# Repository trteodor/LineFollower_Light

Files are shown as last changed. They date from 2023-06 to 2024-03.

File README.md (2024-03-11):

# Light Follower Light

**_ "Robot" which follow for a black line on a white theme _**

⭐ Collecting stars ⭐ - If you liked this project, please leave a star here

Demonstration videos:

Jsumo wheels vs solarbotics:
https://www.youtube.com/watch?v=5hosZAXFKjE

X_Challange 2023, Rzeszow:
https://www.youtube.com/watch?v=OcwFzTCTTZQ

New JSumo Tires test:
https://youtu.be/Sj1vxMwn7Ys (achived average speed 1.8m/s!)

Real world prototypes:    ( Jsumo and Solarbotics wheels )

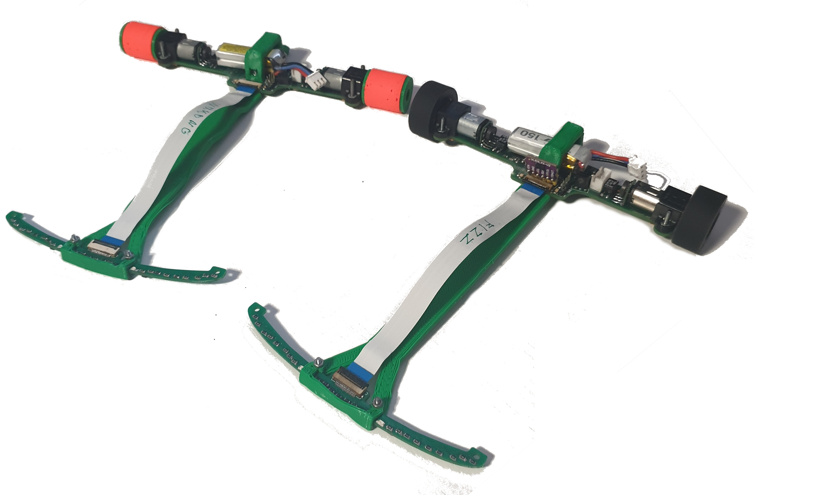
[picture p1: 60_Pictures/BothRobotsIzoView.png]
FristPrototypePhoto


Simulated assembly izometric view:

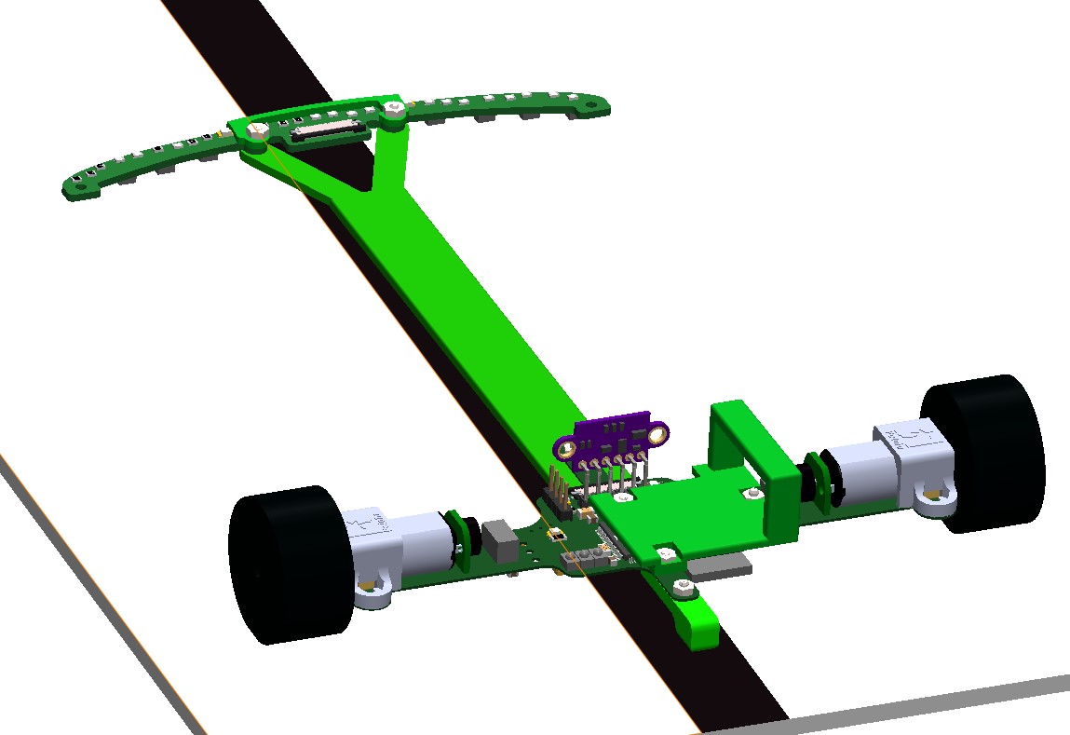
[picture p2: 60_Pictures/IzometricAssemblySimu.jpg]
Izometric3D_View


  * You will need to spend around 200$ if you want recreate this design (PCB order included)
  * most important parts list: 10_PCB_Hardware_Altium\Readme.md

In Embedded source code is implemented many algorithms, PID Controller is used to follow for the black line on white theme.

Nevertheless many things still can be done better. Let's be honest - the prepared Control Code in my opinion is somewhere between a draft and a prototype

# In this project:

PCB and 3D Assemblyis prepared, real world prototype prepared

TODO:
* Add support for MPU-6050
* Add support for VL53l0
* Development of QT service application..
* Generally much things..

# -------------------------------------------------------
The repository contains all the files used to create this project (PCB, Mechanic models, Embedded source Code, QT serv. App code)

QT service app overview screen shot:

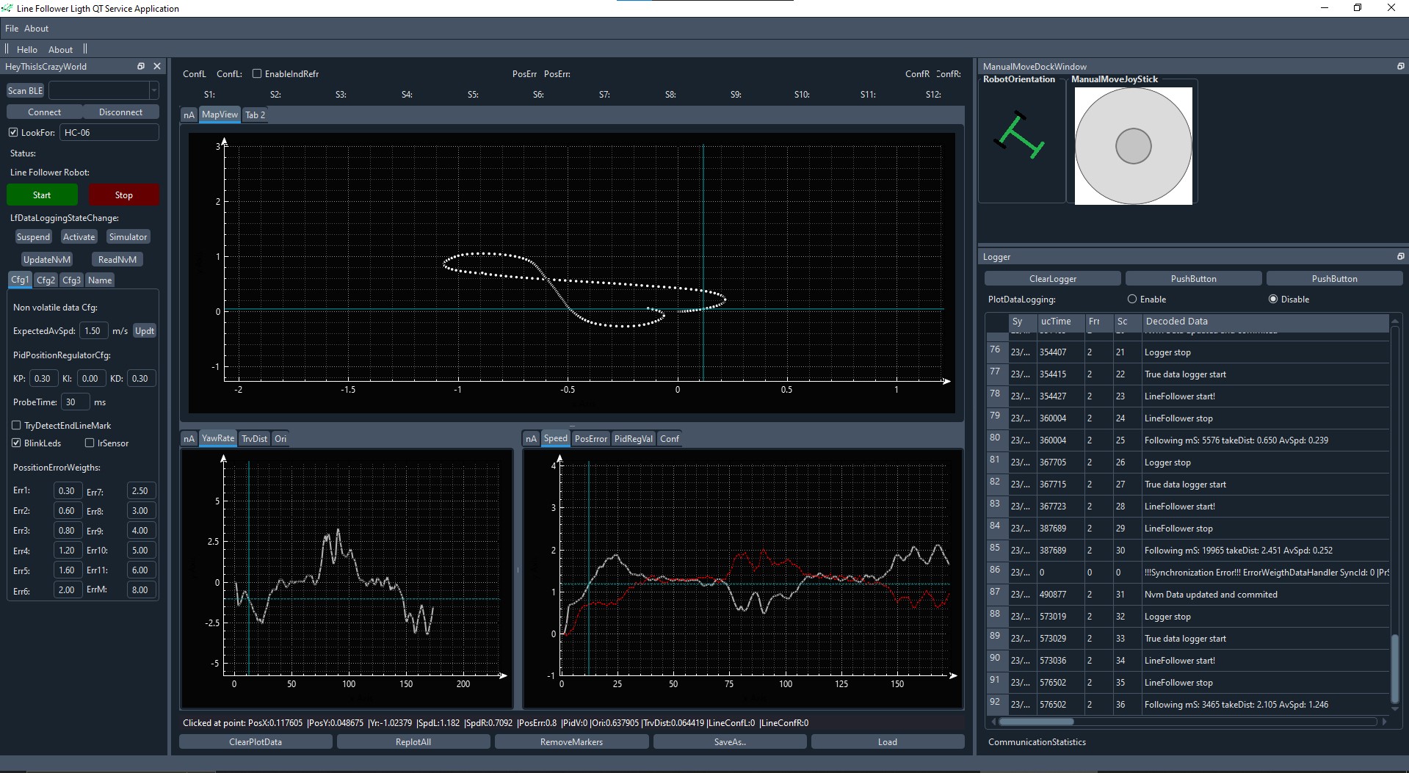
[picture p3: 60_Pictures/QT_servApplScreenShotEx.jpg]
QtApp


Installer wizard:  (created using Inno Compiler)
https://github.com/trteodor/LineFollower_Light/blob/master/40_ServiceApplication_QT/LF_ServiceApp_1.35_Installer.exe

After installation associated "*.lfp" extension should be opened by default by LF_ServiceApp"

Highlevel Overview:

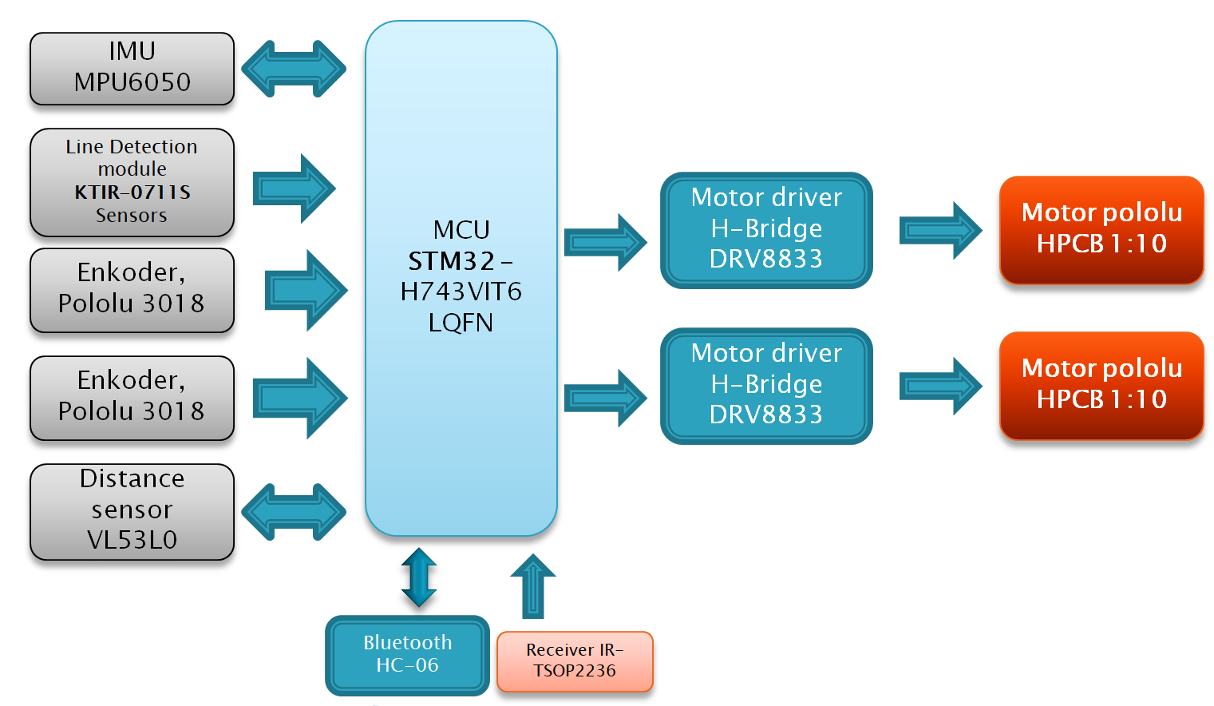
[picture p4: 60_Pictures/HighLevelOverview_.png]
HighLevelOverview


Repository size:

 ~500MB

# References
* https://github.com/trteodor/Line_Follower_STM32H7
* https://forbot.pl/blog/algorytm-linefollowera-c-poczatkujacych-id2722
* https://kcir.pwr.edu.pl/~mucha/Pracki/Jedrzej_Stolarz_praca_inzynierska.pdf
* https://kcir.pwr.edu.pl/~mucha/Pracki/Witek_Lipieta_praca_magisterska.pdf
* https://kcir.pwr.edu.pl/~mucha/Pracki/Rafal_Cyminski_praca_magisterska.pdf
* https://forbot.pl/forum/topic/13552-cukiereczek/

**_If you have questions, please open an issue in this repository or comment below the YouTube video._**

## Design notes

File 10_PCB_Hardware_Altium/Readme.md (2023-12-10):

Altium Designer viewer - is free, use it to view schematics and PCB.

Production files are attached in appropriate folders.

Attached data is sufficient to create production files for PCB (Gerber Files) or for reverse engineering. Modifications to schematics and PCBs are also possible.

Some of the most important items or items not shown in the altium schematics:
* https://botland.com.pl/enkodery/4884-zestaw-enkoderow-magnetycznych-do-micro-silnikow-pololu-kompatybilne-z-hpcb-27-18v-2-szt-pololu-3081.html
* https://botland.com.pl/silniki-dc-micro-z-przekladnia/4974-silnik-hpcb-101-obustronny-wal-pololu-3071.html
* https://www.tme.eu/pl/details/ffc0520150/tasmy-ffc-fpc/riverdi/
* https://www.tme.eu/pl/details/mx-15266-0209/tasmy-ffc-fpc/molex/15266-0209/
* https://botland.com.pl/kola-z-oponami/24-kolo-solarbotics-rw2i-mocowane-wewnetrznie-pololu-1127.html
* https://abc-rc.pl/product-pol-7891-Modul-BMS-PCM-PCB-ladowania-i-ochrony-ogniw-Li-ion-2S-8-4V-5A-18650.html (to get lion protection circuit elements)
* https://botland.com.pl/akumulatory-li-pol-2s-74v-/8973-pakiet-li-pol-dualsky-250mah-30c-2s-74v-eco-s-6941047104631.html or
* https://botland.com.pl/akumulatory-li-pol-2s-74v-/8248-pakiet-li-pol-dualsky-150mah-30c-2s-74v-eco-s-6941047106321.html 
* https://www.tme.eu/pl/details/cmj2101/dlawiki-smd-pozostale/talema/cmj-2-101/
* Distance sensor VL53
* https://kamami.pl/moduly-bluetooth/211365-modul-bluetooth-hc-06-20edr.html

Currently wheels are created using tires ordered here:
* https://www.jsumo.com/js2042-silicone-wheel-without-rim-1-pair
Although, I would recommend you to start with solarbotics wheels

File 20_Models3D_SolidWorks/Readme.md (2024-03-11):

In directory 23_STL are located OutPout files(to print on 3d printer). You can find there relased mechanical 3D STL - files which can be printed using 3D Printer...

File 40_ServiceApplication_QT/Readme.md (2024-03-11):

I'm not familiar with the QT framework, the application is my frist GUI app. Sorry for the style, magic numbers, etc.. 

Despite that, hopefully the source code is readable.

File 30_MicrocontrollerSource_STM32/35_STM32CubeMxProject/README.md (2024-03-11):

To compile MCU Source code you can use STM32CubeIDE or makefiles(GNUmake + arm-none-eabi-gcc)

Used MCU: STM32H743VITx
LQFP100

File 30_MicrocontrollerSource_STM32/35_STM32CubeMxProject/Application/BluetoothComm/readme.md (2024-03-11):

This is Bluetooth low energy module to communicate wirelessly between PC and LineFollower robot

Bluetooth Module: HC-06

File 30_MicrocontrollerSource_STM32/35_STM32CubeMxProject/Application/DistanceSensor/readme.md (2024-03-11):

Not supported(todo)

It's possible to mount a VL53 sensor to detected and omit obstacles.

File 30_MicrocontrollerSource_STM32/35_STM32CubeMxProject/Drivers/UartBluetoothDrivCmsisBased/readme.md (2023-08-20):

Due to some confusion while using HAL libary, it has been decided to implement own simple uart driver to communicate with Bluetooth module.

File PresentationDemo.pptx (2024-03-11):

## My Construction of Line Follower robot

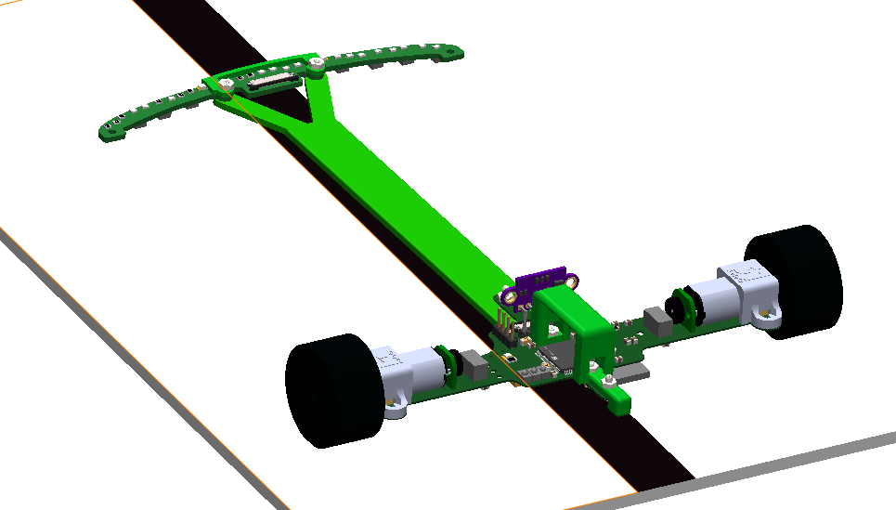
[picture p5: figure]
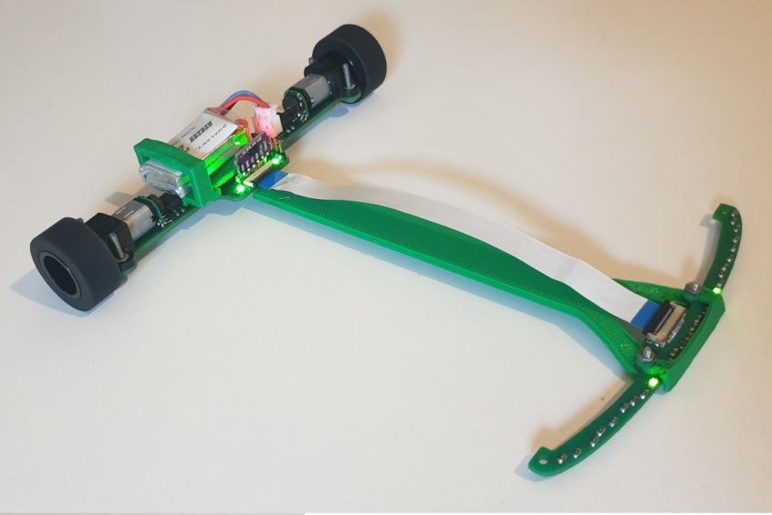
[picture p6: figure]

## Demo video:

Experiments in house environment
- https://www.youtube.com/watch?v=5hosZAXFKjE
Robot competition „X_Challange 2023, Rzeszow”:
- https://www.youtube.com/watch?v=OcwFzTCTTZQ

## Electrical structure:

- The electrical structure of the vehicle model is made from designed printed circuits in Altium Designer:

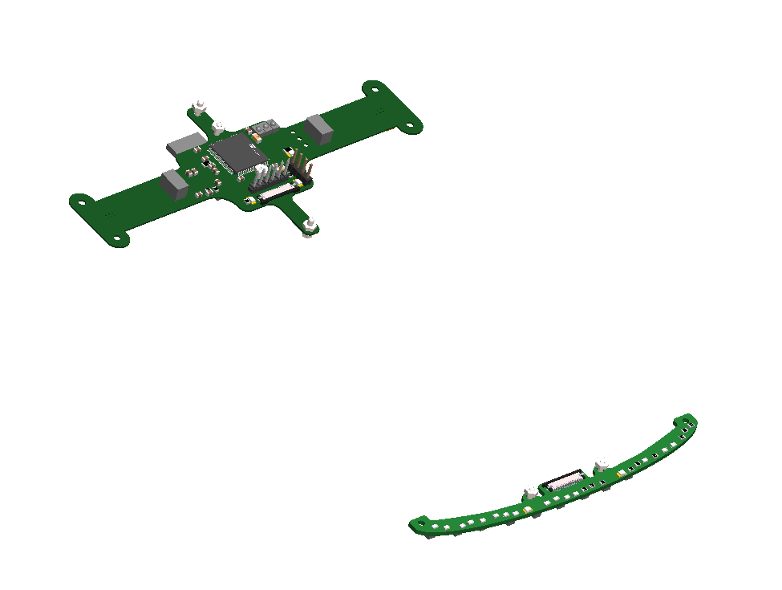
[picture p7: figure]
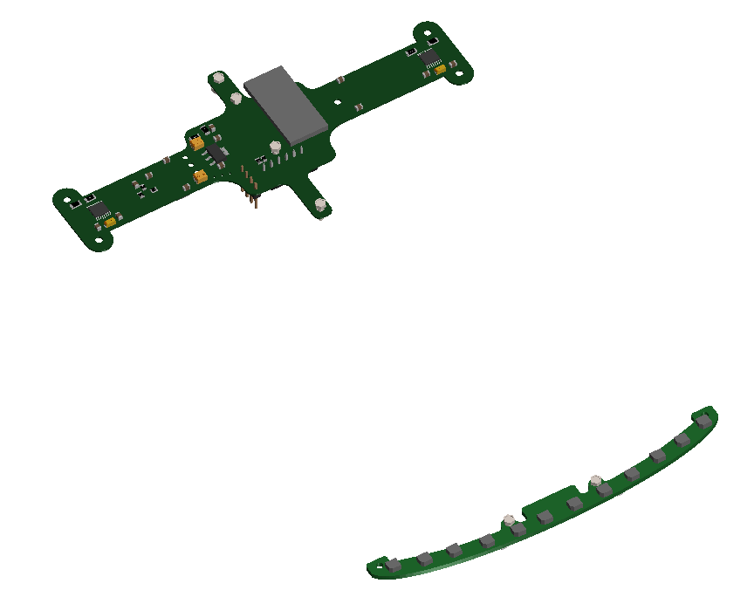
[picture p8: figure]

## Skeleton and connection

- The 3D model of robot has been designed using Solidworks
- In the next step – designed parts were printed on 3D Printer.

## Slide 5

High level overview, hardware blocks

IMU
MPU6050

Line Detection module
KTIR-0711S Sensors

Enkoder,
Pololu 3018

MCU STM32 -H743VIT6
LQFN

Motor driver
H-Bridge
DRV8833

Motor pololu
HPCB 1:10

Enkoder,
Pololu 3018

Motor driver
H-Bridge
DRV8833

Motor pololu
HPCB 1:10

Distance sensor
VL53L0

Bluetooth
HC-06

Receiver IR-
TSOP2236

## Practical realization:

Solarbotics wheels:

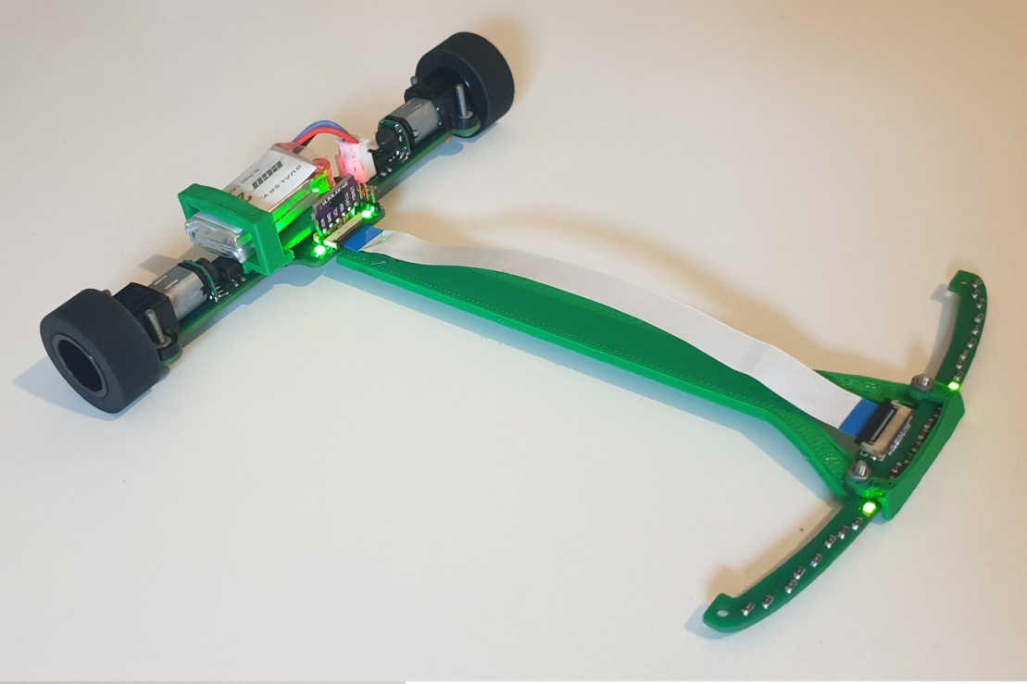
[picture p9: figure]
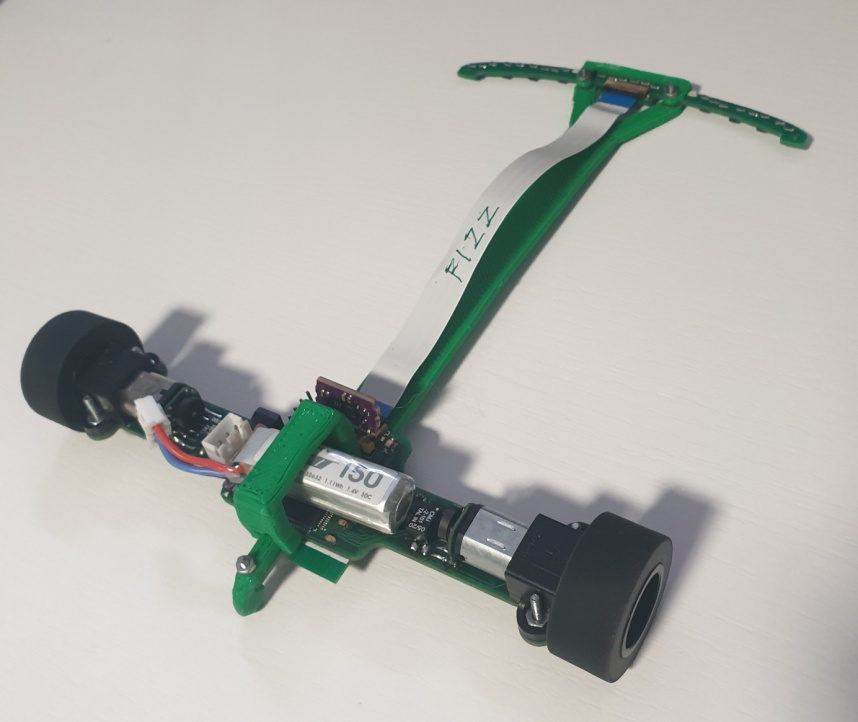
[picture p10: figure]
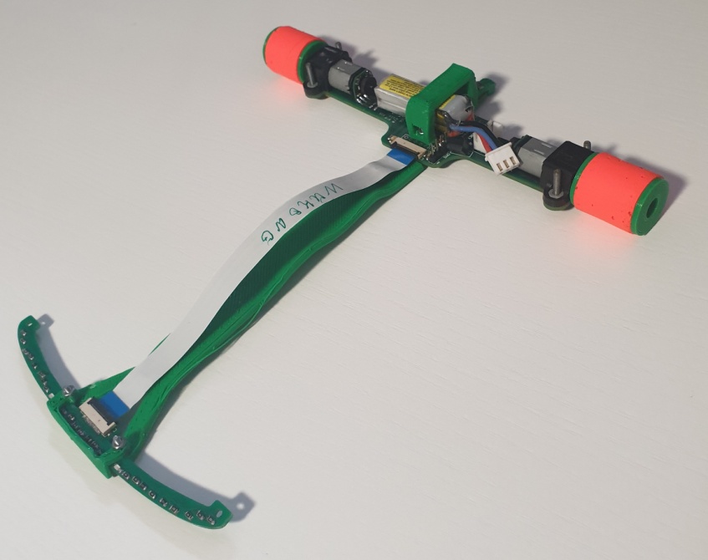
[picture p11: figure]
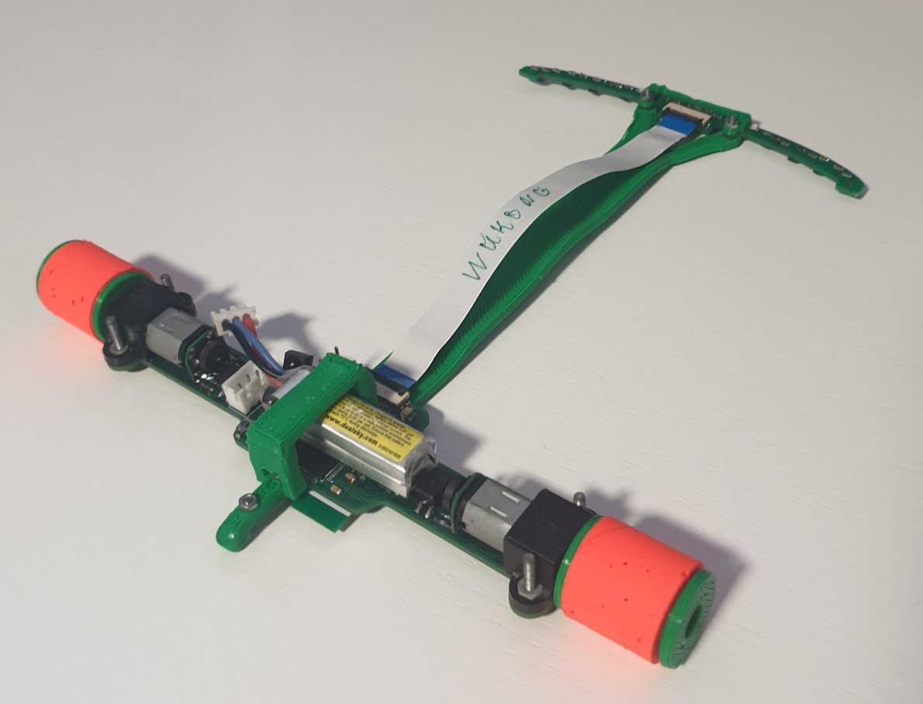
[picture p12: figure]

## Practical realization:

Jsumo wheels:

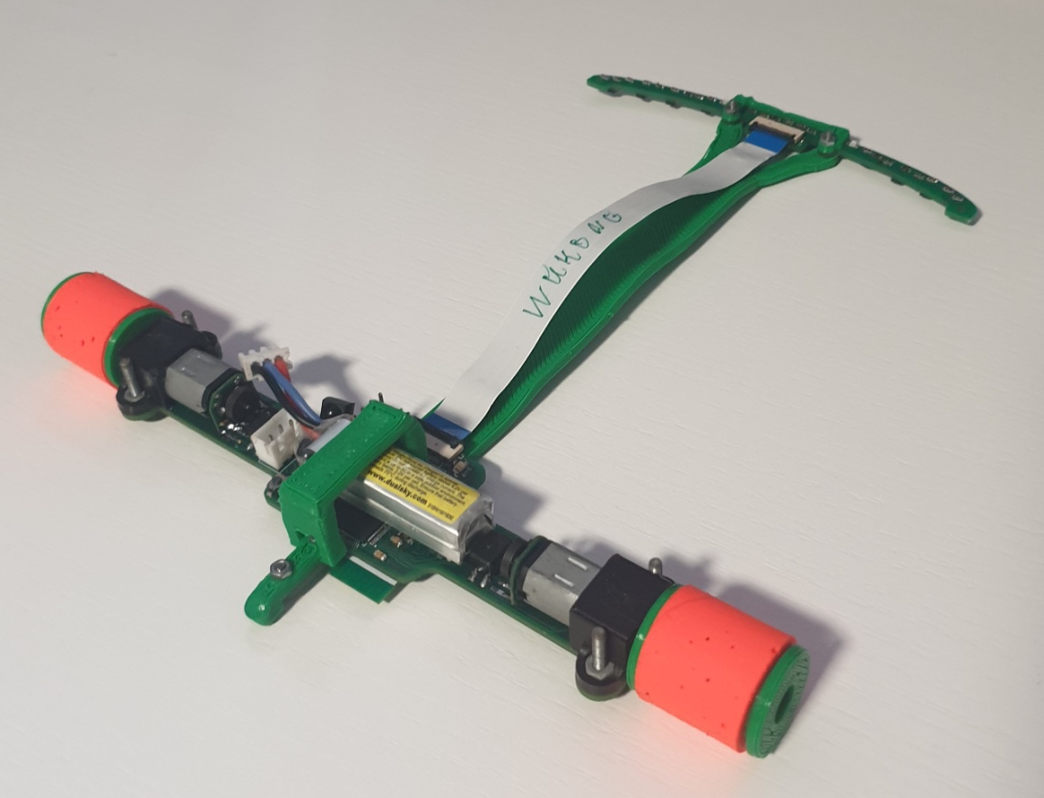
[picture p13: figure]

## Digital representation of the route

- Using the equation below, it is possible to create digital representation of the route.

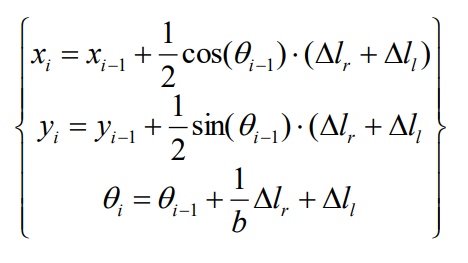
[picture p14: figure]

## Data visualisation, wireless calibration – Windows Desktop App:

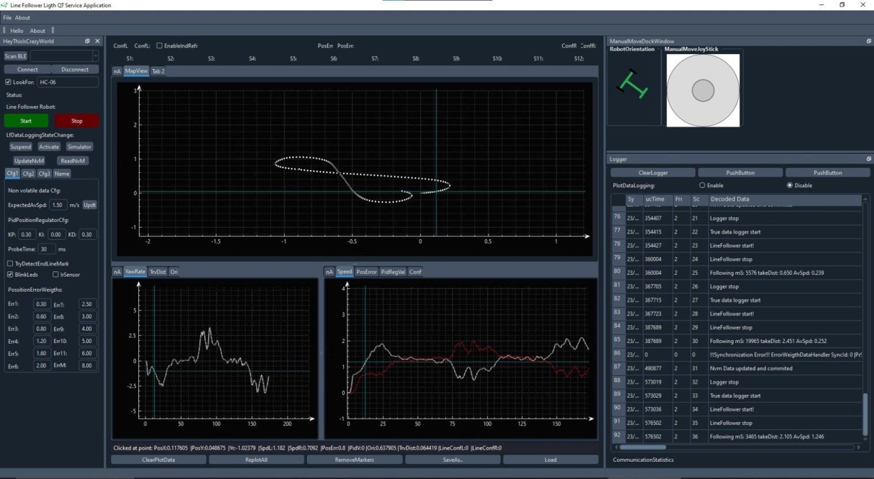
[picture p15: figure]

Designed in QT

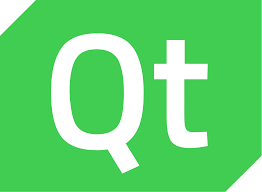
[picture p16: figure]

The app, maybe simply installed:

## It is open source project!

- https://github.com/trteodor/LineFollower_Light
The repository consist:
- MCU Source,
- Schematics, PCB,
- Skeleton(3D elements),
- Documentation,
- everything what is needed to re-create the design/robot.
If you liked the project, please leave a "star" in the repository

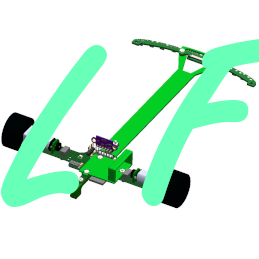
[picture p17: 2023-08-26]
60_Pictures/LF_SimuAsseblyBackSideRightIco.png

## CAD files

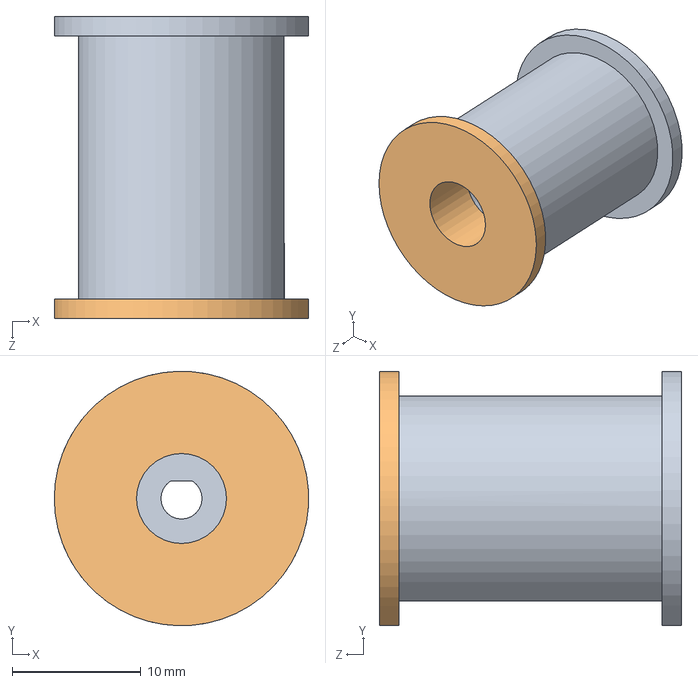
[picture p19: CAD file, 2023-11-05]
20_Models3D_SolidWorks/21_SolidWorksProject/JSummoWheelAsm.SLDASM
19.8 x 19.8 x 23.5 mm
JSumoTireWheel
OutSideCollar

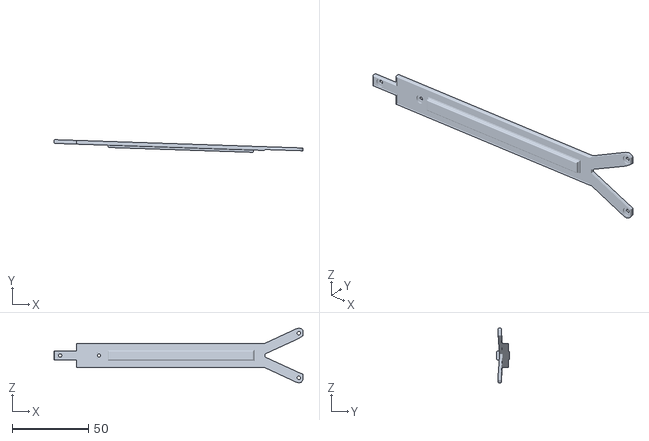
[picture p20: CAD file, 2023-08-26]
20_Models3D_SolidWorks/23_STL - OutPout files( to print on 3d printer)/LF_MB_SB_ConnectorAsm.STL
163.7 x 8.35 x 36.0

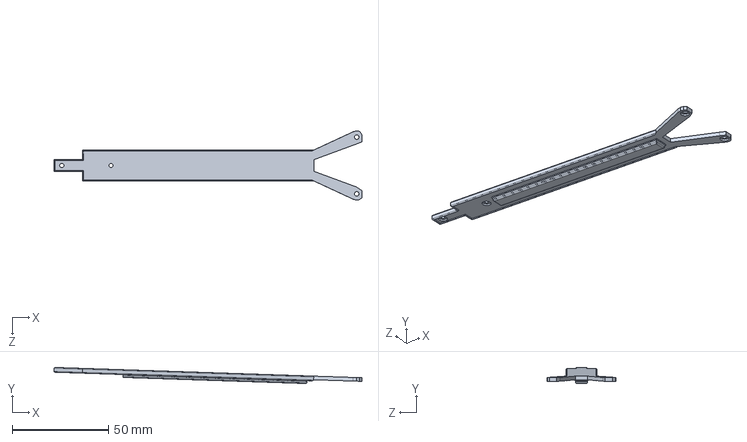
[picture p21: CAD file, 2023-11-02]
20_Models3D_SolidWorks/21_SolidWorksProject/LF_MB_SB_ConnectorAsm.SLDPRT
159.7 x 8.35 x 36.0 mm

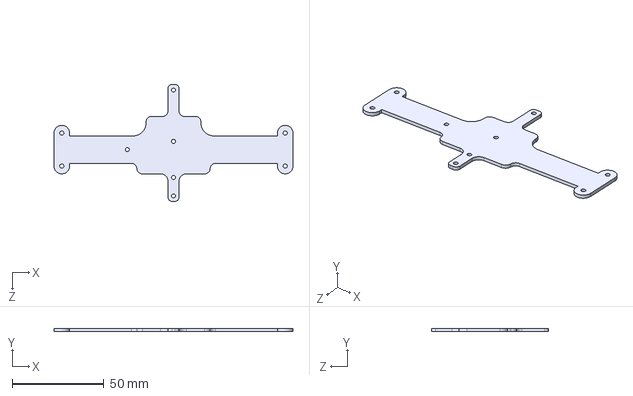
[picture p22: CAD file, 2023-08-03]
20_Models3D_SolidWorks/21_SolidWorksProject/ShapeMainBoardDraft.STEP
130.4 x 1.70 x 63.7 mm

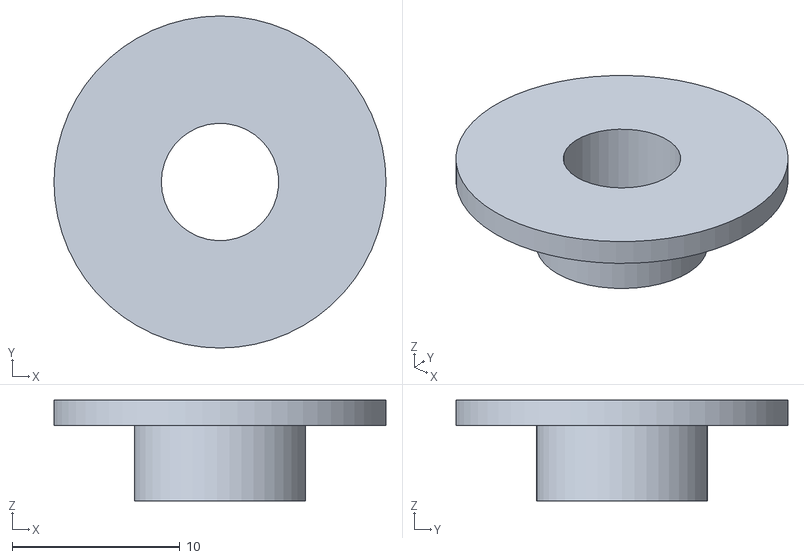
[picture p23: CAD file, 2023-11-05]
20_Models3D_SolidWorks/23_STL - OutPout files( to print on 3d printer)/OutSideCollarJSumoWheel.STL
19.8 x 19.8 x 6.00

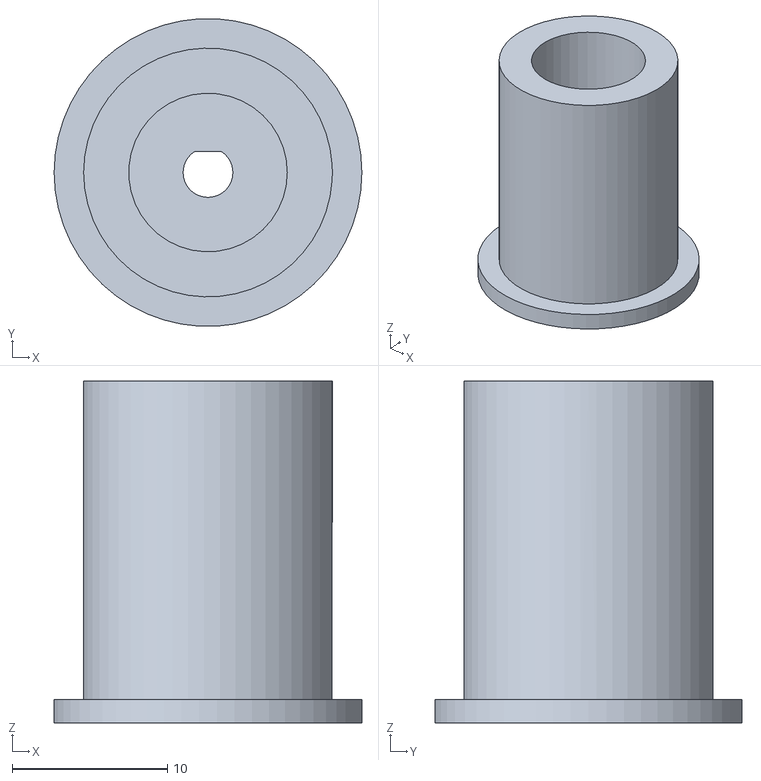
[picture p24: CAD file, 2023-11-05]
20_Models3D_SolidWorks/23_STL - OutPout files( to print on 3d printer)/JSumoTireWheel.STL
19.8 x 19.8 x 22.0

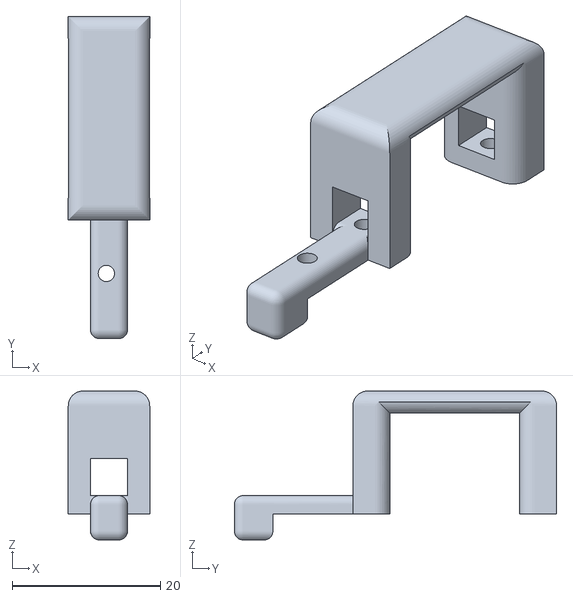
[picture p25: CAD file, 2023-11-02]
20_Models3D_SolidWorks/23_STL - OutPout files( to print on 3d printer)/BatteryHolderJsumo.STL
11.0 x 43.5 x 20.1

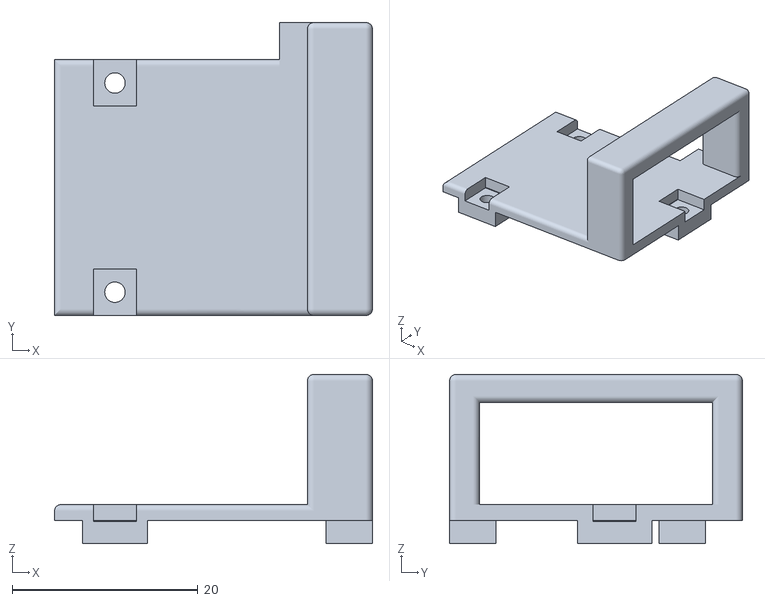
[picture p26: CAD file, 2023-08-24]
20_Models3D_SolidWorks/23_STL - OutPout files( to print on 3d printer)/BatteryHolder.STL
34.2 x 31.5 x 18.2

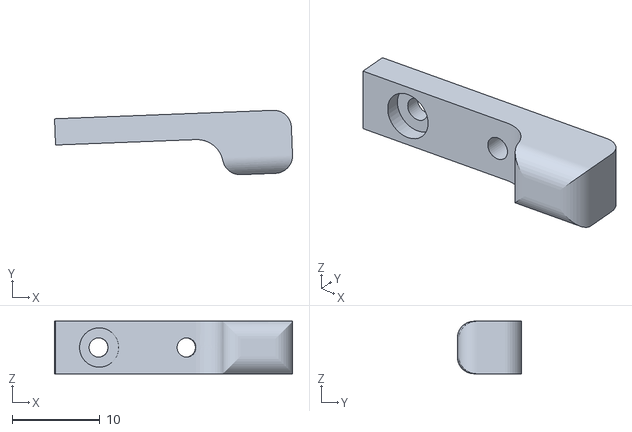
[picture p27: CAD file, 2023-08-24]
20_Models3D_SolidWorks/23_STL - OutPout files( to print on 3d printer)/JumpLiftProtector.STL
27.2 x 7.35 x 6.00

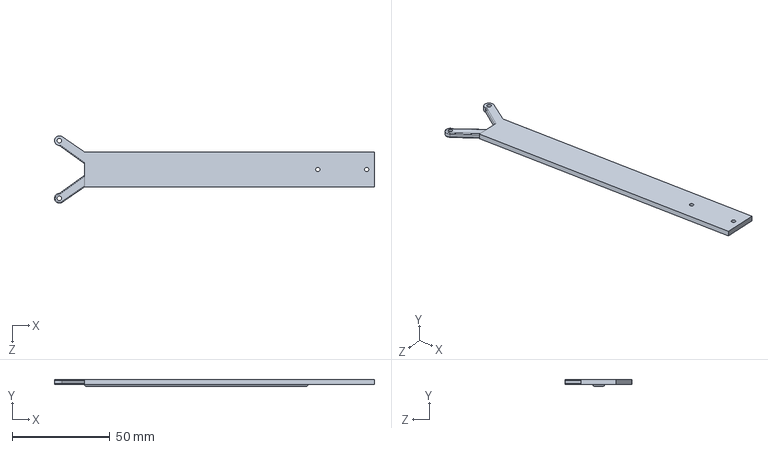
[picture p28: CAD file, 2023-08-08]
20_Models3D_SolidWorks/21_SolidWorksProject/LF_MB_SB_Connector.SLDPRT
163.8 x 3.50 x 34.5 mm

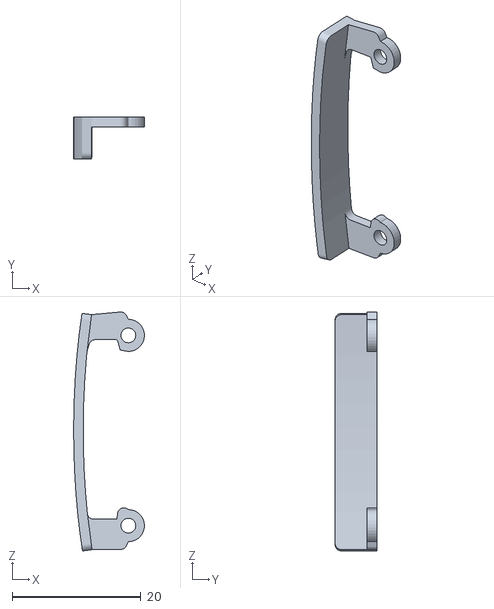
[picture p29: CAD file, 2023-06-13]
20_Models3D_SolidWorks/23_STL - OutPout files( to print on 3d printer)/GroundSlider.STL
11.0 x 6.50 x 37.2

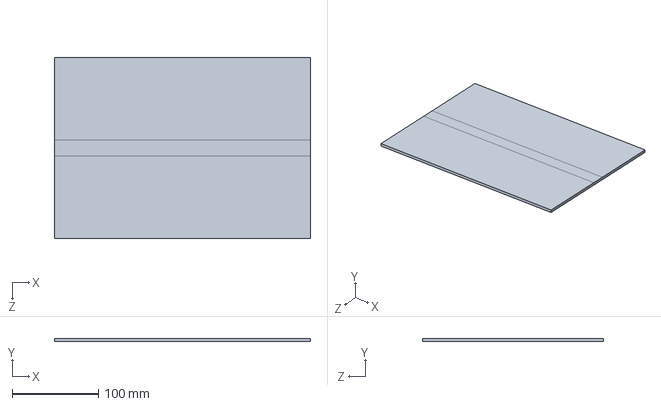
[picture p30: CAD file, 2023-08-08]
20_Models3D_SolidWorks/21_SolidWorksProject/PartOfTruckSimulation.SLDPRT
297.0 x 4.01 x 210.0 mm

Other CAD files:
20_Models3D_SolidWorks/21_SolidWorksProject/OutSideCollar.SLDPRT
20_Models3D_SolidWorks/21_SolidWorksProject/JSumoTireWheel.SLDPRT
20_Models3D_SolidWorks/21_SolidWorksProject/BatteryHolder.SLDPRT
20_Models3D_SolidWorks/21_SolidWorksProject/JumpLiftProtector.SLDPRT
20_Models3D_SolidWorks/21_SolidWorksProject/BatterHolderCl.SLDPRT
20_Models3D_SolidWorks/21_SolidWorksProject/GroundSlider.SLDPRT
20_Models3D_SolidWorks/21_SolidWorksProject/PololuMotorWithEnckodersAndBrackesPlusWheel.STEP
20_Models3D_SolidWorks/21_SolidWorksProject/ShapeMainBoardDraft.SLDPRT
20_Models3D_SolidWorks/21_SolidWorksProject/ShapeSensorBoard.SLDPRT
20_Models3D_SolidWorks/21_SolidWorksProject/ShapeSensorBoard.STEP
20_Models3D_SolidWorks/21_SolidWorksProject/hex head tapping screw_am.SLDPRT
20_Models3D_SolidWorks/21_SolidWorksProject/vl53l0x.STEP

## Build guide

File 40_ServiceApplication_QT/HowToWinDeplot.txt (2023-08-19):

windeployqt.exe --qmldir "...\VirtualJoystickQML" "...\Release_1.1"

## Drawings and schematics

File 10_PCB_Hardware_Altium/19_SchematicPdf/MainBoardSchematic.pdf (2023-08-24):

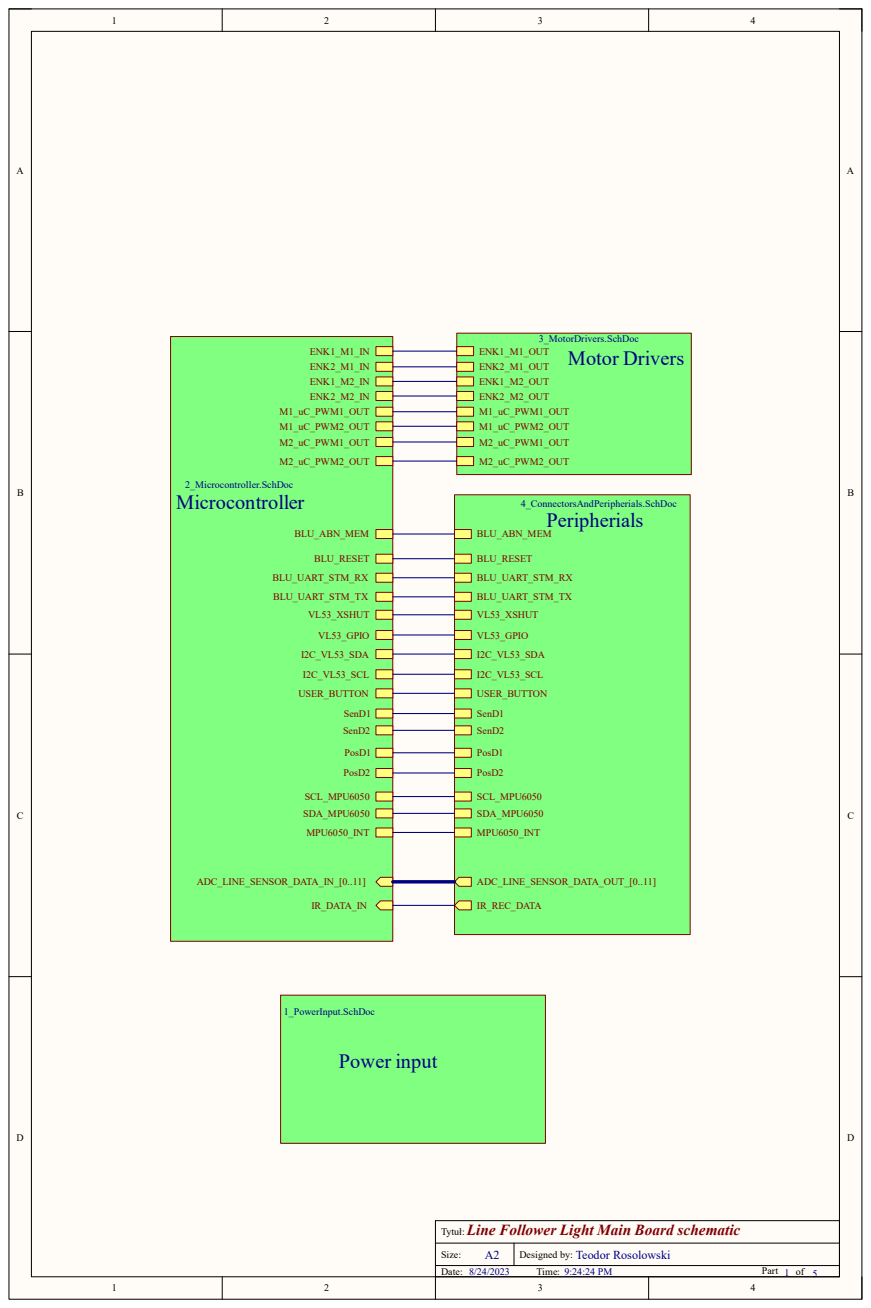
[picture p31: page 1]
Teodor Rosolowski; Size:; Designed by:; Date:; Time:; Part; ENK1_M1_OUT ENK2_M1_OUT ENK1_M2_OUT; M2_uC_PWM1_OUT; ENK2_M2_OUT M1_uC_PWM1_OUT M1_uC_PWM2_OUT; M2_uC_PWM2_OUT; Motor Drivers; 3_MotorDrivers.SchDoc; ADC_LINE_SENSOR_DATA_IN_[0..11]; IR_DATA_IN; MPU6050_INT; SDA_MPU6050; ENK2_M2_IN; ENK1_M2_IN; M1_uC_PWM1_OUT M1_uC_PWM2_OUT; BLU_RESET; BLU_ABN_MEM; ENK1_M1_IN; BLU_UART_STM_TX; ENK2_M1_IN; I2C_VL53_SCL; SenD1; PosD2; SCL_MPU6050; BLU_UART_STM_RX; SenD2; PosD1; VL53_GPIO; VL53_XSHUT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

Line Follower Light Main Board schematic
Tytuł:

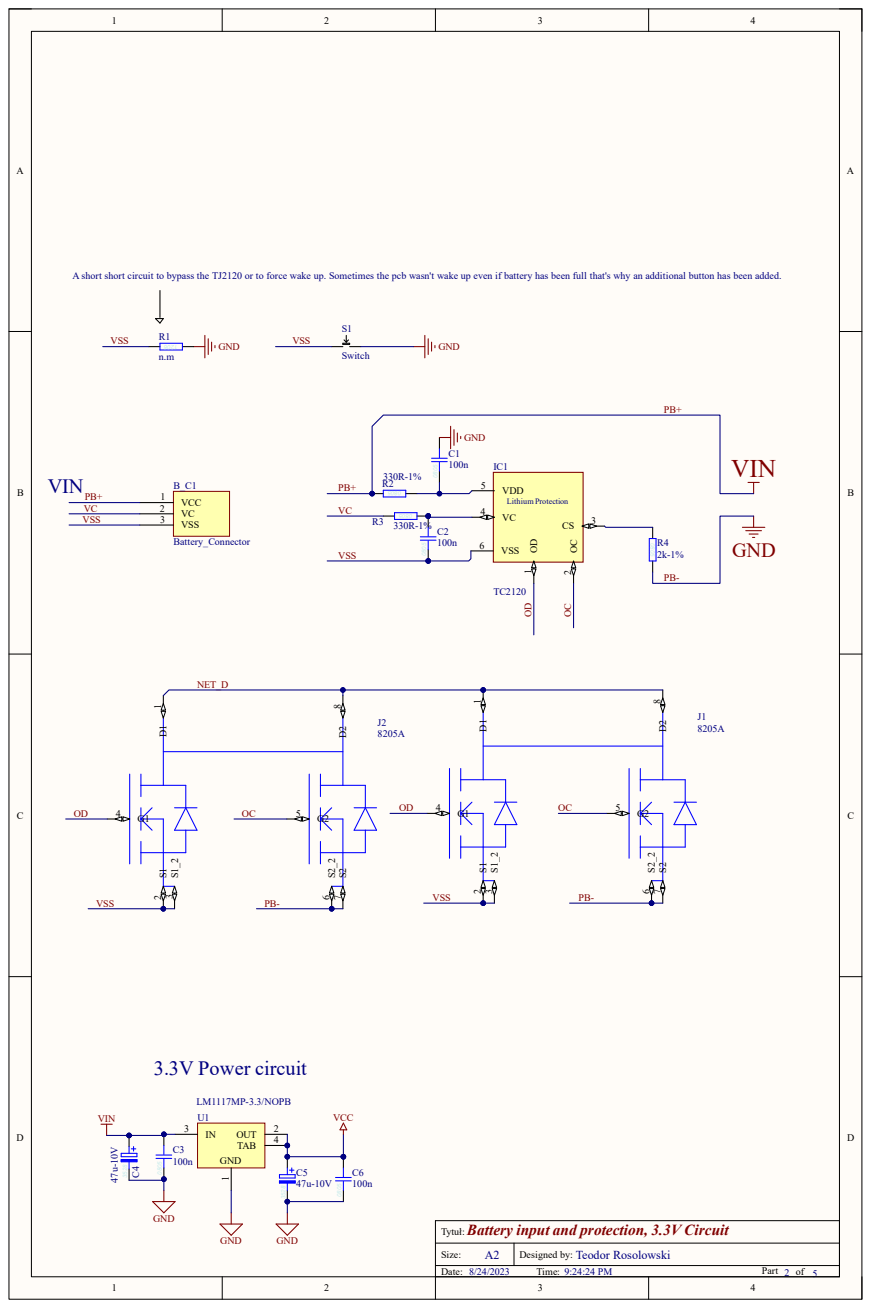
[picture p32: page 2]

A short short circuit to bypass the TJ2120 or to force wake up. Sometimes the pcb wasn't wake up even if battery has been full that's why an additional button has been added.

Battery input and protection, 3.3V Circuit

# USER_BTN 0805

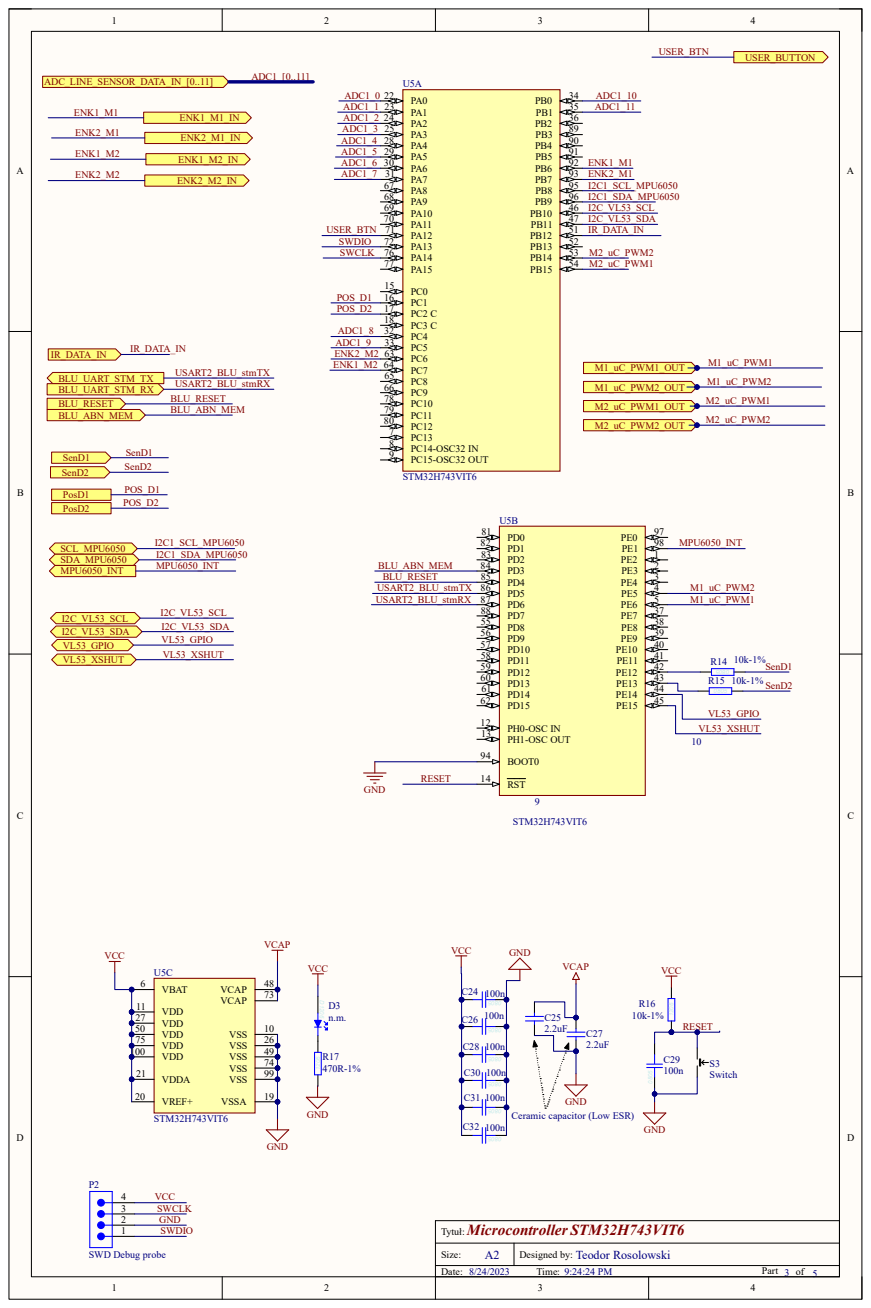
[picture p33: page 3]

Ceramic capacitor (Low ESR)

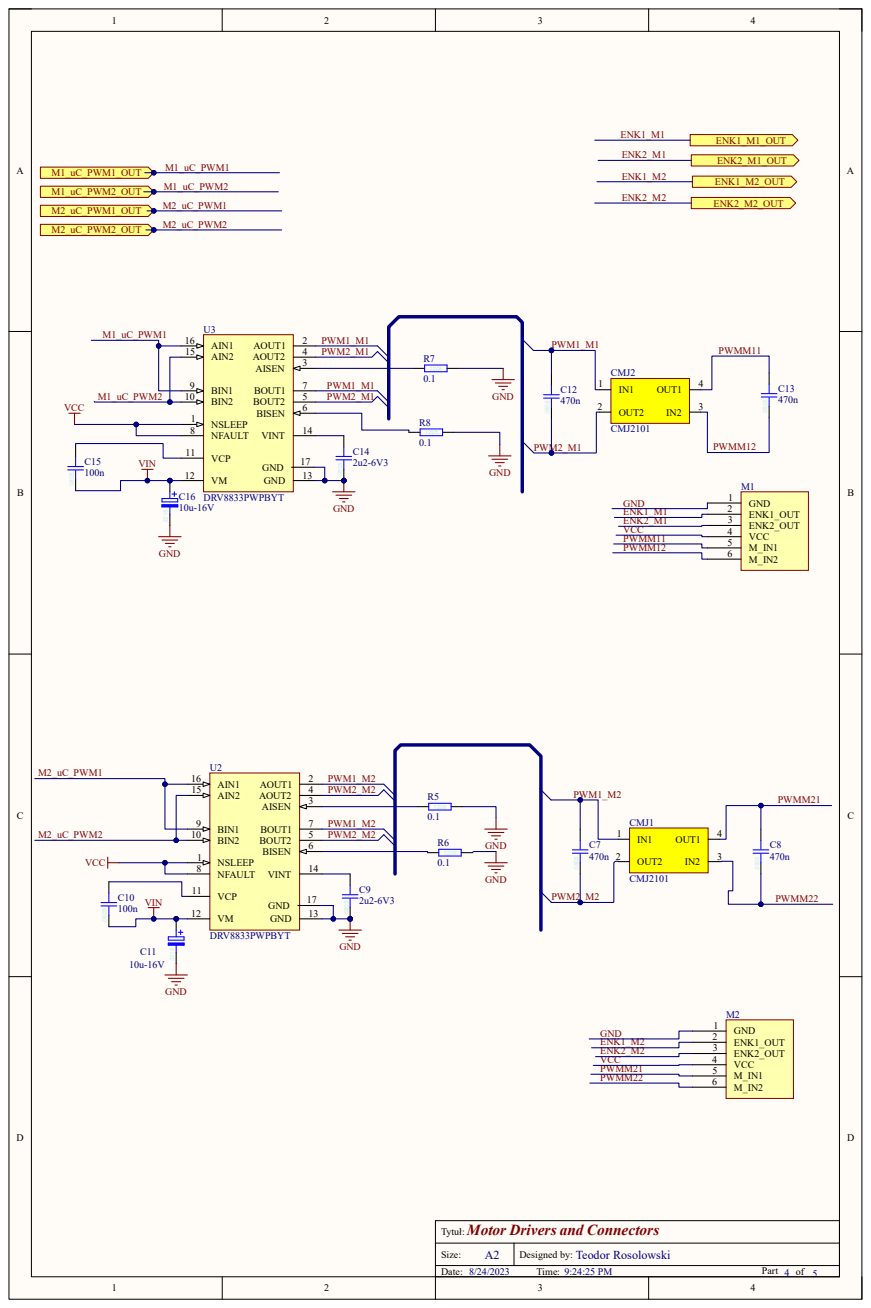
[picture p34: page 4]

Motor Drivers and Connectors

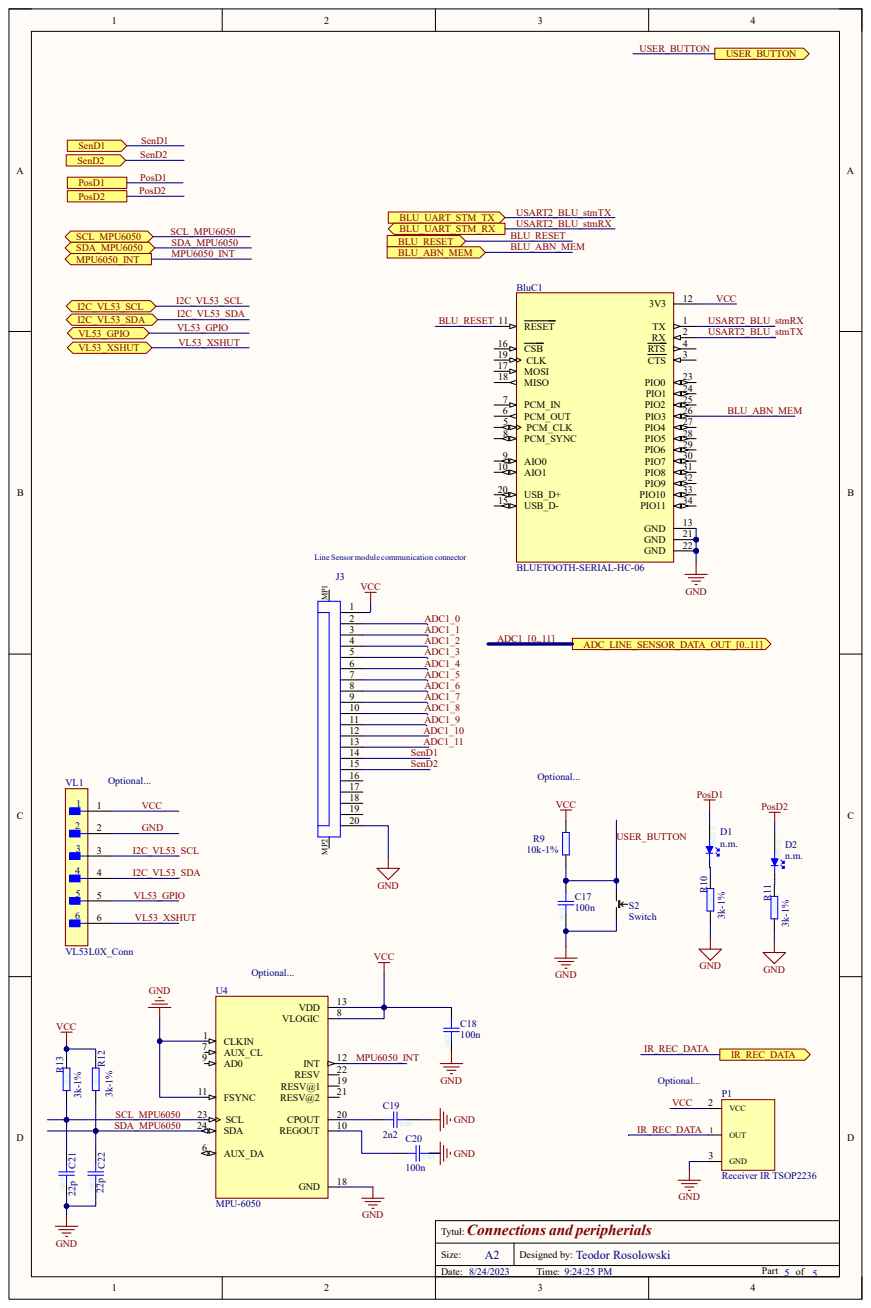
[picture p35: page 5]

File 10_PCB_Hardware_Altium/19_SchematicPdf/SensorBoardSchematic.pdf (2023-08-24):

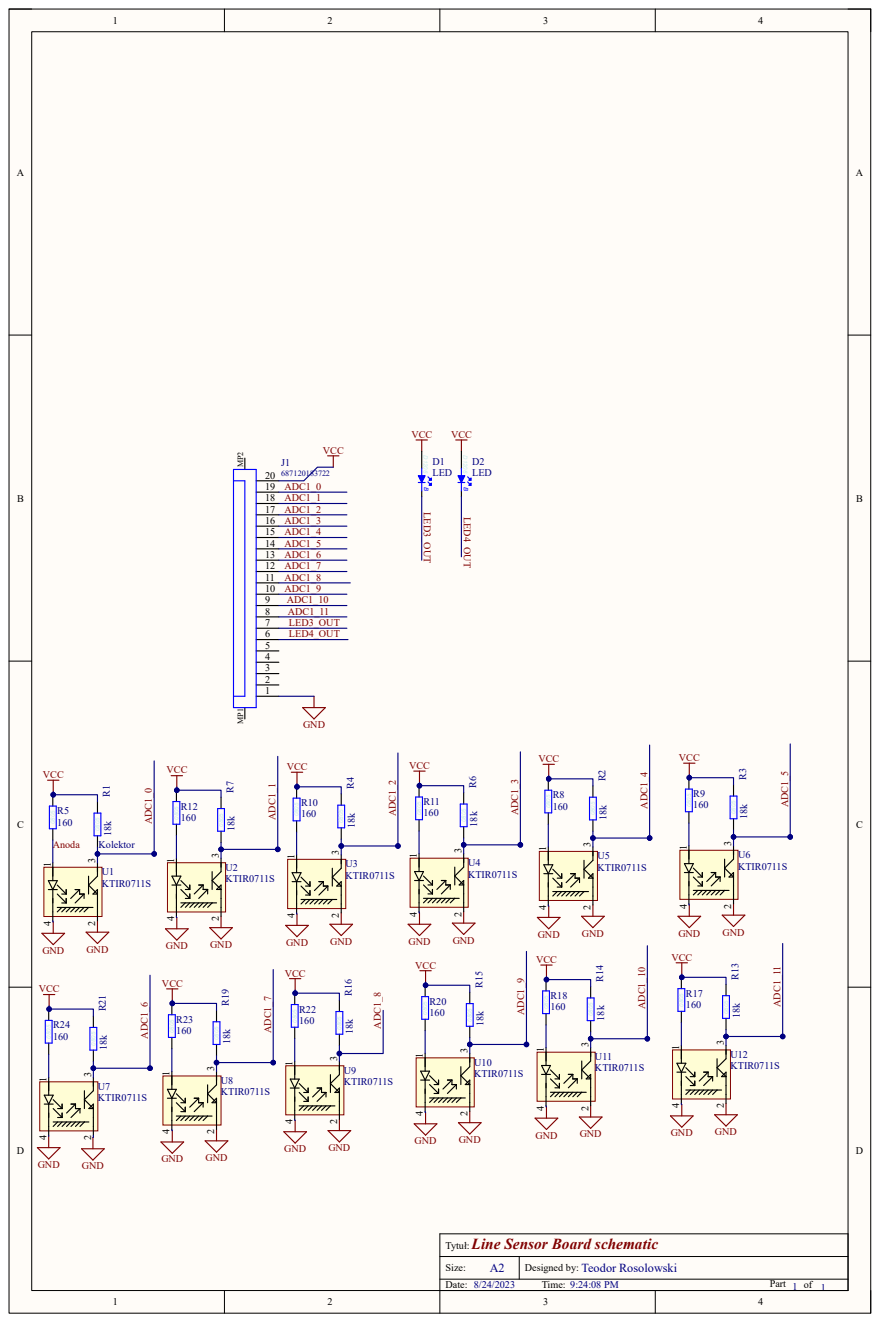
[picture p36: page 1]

Line Sensor Board schematic
Tytuł:

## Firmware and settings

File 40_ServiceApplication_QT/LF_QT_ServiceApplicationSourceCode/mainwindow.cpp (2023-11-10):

#include "mainwindow.h"
#include "ui_mainwindow.h"

#include <QtQuick/QQuickView>
#include <QtQuick/QQuickItem>
#include <QUrl>

#include <QFile>
#include <QJsonArray>
#include <QJsonDocument>

/**************************************************************/
MainWindow::MainWindow(QWidget *parent)
    : QMainWindow(parent)
    , ui(new Ui::MainWindow)
{
    QThread::currentThread()->setObjectName("Main Window Thread");

    ui->setupUi(this);

    this->setWindowTitle("Line Follower Ligth QT Service Application");


    /*All declared plots/ graph must be initialized!!!*/
    PlotMap.LfGraphInitialize(ui->MapViewWidget,QCPGraph::lsNone);
    PlotYawRate.LfGraphInitialize(ui->PlotYawRateW,QCPGraph::lsLine);
    PlotSpd.LfGraphInitialize(ui->PlotSpdW,QCPGraph::lsLine);
    PlotPosErr.LfGraphInitialize(ui->PlotPosErrW,QCPGraph::lsLine);
    PlotPidRegVal.LfGraphInitialize(ui->PlotPidRegValW,QCPGraph::lsLine);
    PlotTrvDistance.LfGraphInitialize(ui->PlotTrvDistanceW,QCPGraph::lsLine);
    PlotOrientation.LfGraphInitialize(ui->PlotOrientationW,QCPGraph::lsLine);
    PlotLinePosConfidence.LfGraphInitialize(ui->PlotLinePosConfW,QCPGraph::lsLine);

    connect(&PlotMap, SIGNAL(LfGraphSignal_graphClicked(int)), this, SLOT(MainWinPlot_DrawMarkersAtDataIndexInfo(int) ));
    connect(&PlotYawRate, SIGNAL(LfGraphSignal_graphClicked(int)), this, SLOT(MainWinPlot_DrawMarkersAtDataIndexInfo(int) ));
    connect(&PlotSpd, SIGNAL(LfGraphSignal_graphClicked(int)), this, SLOT(MainWinPlot_DrawMarkersAtDataIndexInfo(int) ));
    connect(&PlotPosErr, SIGNAL(LfGraphSignal_graphClicked(int)), this, SLOT(MainWinPlot_DrawMarkersAtDataIndexInfo(int) ));
    connect(&PlotPidRegVal, SIGNAL(LfGraphSignal_graphClicked(int)), this, SLOT(MainWinPlot_DrawMarkersAtDataIndexInfo(int) ));
    connect(&PlotTrvDistance, SIGNAL(LfGraphSignal_graphClicked(int)), this, SLOT(MainWinPlot_DrawMarkersAtDataIndexInfo(int) ));
    connect(&PlotOrientation, SIGNAL(LfGraphSignal_graphClicked(int)), this, SLOT(MainWinPlot_DrawMarkersAtDataIndexInfo(int) ));
    connect(&PlotLinePosConfidence, SIGNAL(LfGraphSignal_graphClicked(int)), this, SLOT(MainWinPlot_DrawMarkersAtDataIndexInfo(int) ));


    /*Initialize all needed connections for Bluetooth Data Manager*/
    BLU_InitializeQTConnections();
    ConfigureTextLineAndNvMConnections();


    addJoyStick(ui->RobotMoverXYGridLayout);


    /*Debug Table configure*/
    ui->DebugDataTable->setRowCount(0);
    ui->DebugDataTable->setColumnWidth(0,10);
    ui->DebugDataTable->setColumnWidth(1,10);
    ui->DebugDataTable->setColumnWidth(2,10);
    ui->DebugDataTable->setColumnWidth(3,10);
    ui->DebugDataTable->setColumnWidth(4,600);
    ui->DebugDataTable->horizontalHeader()->setDefaultAlignment(Qt::AlignLeft);


    QPalette pal = ui->BLU_RobotStart_Button->palette();
    pal.setColor(QPalette::Button, QColor(Qt::blue));
    ui->BLU_RobotStart_Button->setAutoFillBackground(true);
    ui->BLU_RobotStart_Button->setPalette(pal);
    ui->BLU_RobotStart_Button->update();


    MainWin_DrawOrientationIndicator( 3.14F / 2.0F);

    /*Initialize dark theme*/
    QFile f(":qdarkstyle/dark/darkstyle.qss");

    if (!f.exists())   {
        qDebug() << "Unable to set stylesheet, file not found\n";
    }

    else   {
        f.open(QFile::ReadOnly | QFile::Text);
        QTextStream ts(&f);
        qApp->setStyleSheet(ts.readAll());
    }


    QSettings settings("LfServiceApp", "BluDeviceName");
//    settings.setValue("CurrDeviceName", "Franek");
    QVariant CurrDevName = settings.value("CurrDeviceName");
    QString NewLineEditText = CurrDevName.toString();
//    qDebug() << NewLineEditText ;

    ui->BLU_AutoConnDevNameL->setText(NewLineEditText);


//    if(qApp->arguments().count() > 0)
//    {
//        qDebug() << "argumentsCount" << qApp->arguments().at(0);
//    }

    if(qApp->arguments().count() > 1  && qApp->arguments().at(1).endsWith(".lfp") ==true)
    {
        CurrentLfProjectFilePath = qApp->arguments().at(1);
        QString LoadedProjectInfo = QString("DataLoadedFromProjectFile: %1").arg(CurrentLfProjectFilePath);
        MainWin_DebugTable_InsertDataRow(0, 0, 0, LoadedProjectInfo);

        LoadDataLineFollowerProjecrOrJson(CurrentLfProjectFilePath);
    }
}


/*********************************************************************************************************/
MainWindow::~MainWindow()
{
    on_BLU_SimulatorSuspendButton_clicked();
    QThread::msleep(25);
    on_BLU_SimulatorSuspendButton_clicked();
    QThread::msleep(25);
    on_BLU_SimulatorSuspendButton_clicked();
    QThread::msleep(25);
    /*Send the command 3x to be sure that fakeProducer will be stopped, if not then re-connection may be impossible
     * - HW reset may be required
    */

//    TODO: Veriyfy? emit BLU_DisconnectDevice();

    QSettings settings("LfServiceApp", "BluDeviceName");
    QString NewSearchedBluDeviceName = ui->BLU_AutoConnDevNameL->text();
    settings.setValue("CurrDeviceName", NewSearchedBluDeviceName);

    delete ui;

    qDebug("Reached end");
}

void MainWindow::changeEvent( QEvent* e )
{
    if( e->type() == QEvent::WindowStateChange )
    {
        qDebug() << "this->windowState()" << this->windowState();

        QWindowStateChangeEvent* event = static_cast< QWindowStateChangeEvent* >( e );

        if( event->oldState() & Qt::WindowMinimized )
        {
            qDebug() << "Window restored (to normal or maximized state)!";
        }
        else if( event->oldState() == Qt::WindowNoState && this->windowState() == Qt::WindowMaximized )
        {
            qDebug() << "Window Maximized!";

        }
        else if(this->windowState() == Qt::WindowNoState && event->oldState() == Qt::WindowMaximized){
            qDebug() << "Window restored to normal from maximazed state";
        }
    }
}

void MainWindow::addJoyStick(QLayout *layout_, JoyType type)
{
    QQuickView *view = new QQuickView();
    /* NB: We load the QML from a .qrc file becuase the Qt build step
     * that packages the final .app on Mac forgets to add the QML
     * if you reference it directly
     */
    view->setSource(QUrl("qrc:/res/virtual_joystick.qml"));

    /* Enable transparent background on the QQuickView
     * Note that this currently does not work on Windows
     */
#ifndef _WIN32
    view->setClearBeforeRendering(true);
    view->setColor(QColor(Qt::transparent));
#endif

    // Attach to the 'mouse moved' signal
    auto *root = view->rootObject();
    if (type == HorizontalOnly)
        root->setProperty("horizontalOnly", true);
    else if (type == VerticalOnly)
        root->setProperty("verticalOnly", true);
    connect(
        root,
        SIGNAL(joystick_moved(double, double)),
        this,
        SLOT(joystick_moved(double, double))
        );

    // Create a container widget for the QQuickView
    QWidget *container = QWidget::createWindowContainer(view, this);
    container->setMinimumSize(160, 160);
    container->setMaximumSize(160, 160);
    container->setFocusPolicy(Qt::TabFocus);
    layout_->addWidget(container);
}

/**
 * @brief MainWindow::mouse_moved Called when the virtual joystick is moved
 * @param x Mouse x position
 * @param y Mouse y position
 */
void MainWindow::joystick_moved(double x, double y) {

    float VecValX= (float)x;
    float VecValY= (float)y;
    char command[BLU_SINGLE_TR_MESSAGE_SIZE-2];

    command[0] = (char)BluDataManager::BLU_NvM_ManualCntrlCommand;
    std::memcpy(&command[2],  &VecValX, sizeof(float));
    std::memcpy(&command[6],  &VecValY, sizeof(float));

    QByteArray Helper = QByteArray::fromRawData(command,BLU_SINGLE_TR_MESSAGE_SIZE -2);
    Helper.append("\n\r");
    BluInputDataProcessingWrapper.bleutoothClassicConnection.bluetoothSendDataToDevice(Helper);

//Debug/ test
//    float ExpectedOrientation = ( (float)atan2(VecValY,VecValX) );
//    if(ExpectedOrientation < (0.0F) ){
//        ExpectedOrientation =  (3.14) + (3.14 - fabs(ExpectedOrientation));
//        /*To get full circle*/
//    }
//    MainWin_DrawOrientationIndicator(ExpectedOrientation);

    //qDebug() << "VecValX:" << VecValX << "VecValY: " << VecValY;
}

void MainWindow::ConfigureTextLineAndNvMConnections(void)
{
    dblValidator.setNotation(QDoubleValidator::StandardNotation);
    dblValidator.setLocale(QLocale::C);

    ui->ErrW1_Text->setValidator(&dblValidator);
    ui->ErrW2_Text->setValidator(&dblValidator);
    ui->ErrW3_Text->setValidator(&dblValidator);
    ui->ErrW4_Text->setValidator(&dblValidator);
    ui->ErrW5_Text->setValidator(&dblValidator);
    ui->ErrW6_Text->setValidator(&dblValidator);
    ui->ErrW7_Text->setValidator(&dblValidator);
    ui->ErrW8_Text->setValidator(&dblValidator);
    ui->ErrW9_Text->setValidator(&dblValidator);
    ui->ErrW10_Text->setValidator(&dblValidator);
    ui->ErrW11_Text->setValidator(&dblValidator);
    ui->ErrWM_Text->setValidator(&dblValidator);

    ui->ExpectedAvSpdText->setValidator(&dblValidator);
    ui->PID_KP_text->setValidator(&dblValidator);
    ui->PID_KI_text->setValidator(&dblValidator);
    ui->PID_KD_text->setValidator(&dblValidator);
    ui->ProbeTimeText->setValidator(&dblValidator);

    ui->TextWheelBase->setValidator(&dblValidator);
    ui->TextOneImpDist->setValidator(&dblValidator);

    ui->textRightAgKp->setValidator(&dblValidator);
    ui->textRightAgKd->setValidator(&dblValidator);
    ui->textRightAgBaseSpd->setValidator(&dblValidator);
    ui->textRightAgMaxYr->setValidator(&dblValidator);
    ui->textRightBrThr->setValidator(&dblValidator);
    ui->textRightBrTim->setValidator(&dblValidator);
    ui->textStrghtLineMinLght->setValidator(&dblValidator);
    ui->textStrghtLineMaxYawRate->setValidator(&dblValidator);
    ui->textRightAgPrTim->setValidator(&dblValidator);

    ui->TextPwmToSpAFacL->setValidator(&dblValidator);
    ui->TextPwmToSpAFacR->setValidator(&dblValidator);
    ui->TextPwmToSpBFacL->setValidator(&dblValidator);
    ui->TextPwmToSpBFacR->setValidator(&dblValidator);

    ui->SpdProfileTrvD1->setValidator(&dblValidator);
    ui->SpdProfileTrvD2->setValidator(&dblValidator);
    ui->SpdProfileTrvD3->setValidator(&dblValidator);
    ui->SpdProfileTrvD4->setValidator(&dblValidator);
    ui->SpdProfileTrvD5->setValidator(&dblValidator);
    ui->SpdProfileTrvD6->setValidator(&dblValidator);
    ui->SpdProfileTrvD7->setValidator(&dblValidator);
    ui->SpdProfileTrvD8->setValidator(&dblValidator);
    ui->SpdProfileTrvD9->setValidator(&dblValidator);
    ui->SpdProfileTrvD10->setValidator(&dblValidator);
    ui->SpdProfileTrvD11->setValidator(&dblValidator);

    ui->SpdProfileBspd1->setValidator(&dblValidator);
    ui->SpdProfileBspd2->setValidator(&dblValidator);
    ui->SpdProfileBspd3->setValidator(&dblValidator);
    ui->SpdProfileBspd4->setValidator(&dblValidator);
    ui->SpdProfileBspd5->setValidator(&dblValidator);
    ui->SpdProfileBspd6->setValidator(&dblValidator);
    ui->SpdProfileBspd7->setValidator(&dblValidator);
    ui->SpdProfileBspd8->setValidator(&dblValidator);
    ui->SpdProfileBspd9->setValidator(&dblValidator);
    ui->SpdProfileBspd10->setValidator(&dblValidator);
    ui->SpdProfileBspd11->setValidator(&dblValidator);

    connect(&NvM_ErrWeigthUpdateDelayTimer, SIGNAL(timeout()), this, SLOT(NvM_ErrWeigthUpdateDelayTimerTimeout()));
    connect(&NvM_PidDatahUpdateDelayTimer, SIGNAL(timeout()), this, SLOT(NvM_PidDatahUpdateDelayTimerTimeout()));
    connect(&NvM_rAgDatahUpdateDelayTimer, SIGNAL(timeout()), this, SLOT(NvM_rAgDatahUpdateDelayTimerTimeout()));
    connect(&NvM_VehCfghUpdateDelayTimer, SIGNAL(timeout()), this, SLOT(NvM_VehCfgDataUpdateDelayTimerTimeout()));
    connect(&NvM_MotorsFactorsUpdateDelayTimer, SIGNAL(timeout()), this, SLOT(NvM_MotorsFactorsDataUpdateDelayTimerTimeout()));
    connect(&NvM_EncoderCfgUpdateDelayTimer, SIGNAL(timeout()), this, SLOT(NvM_EncodersConfigDataUpdateDelayTimerTimeout()));
    connect(&NvM_SpeedProfileUpdateDelayTimer, SIGNAL(timeout()), this, SLOT(NvM_ProfileSpeedConfigDataUpdateDelayTimerTimeout()));

}



/*********************************************************************************************************/
/*********************************************************************************************************/
/*********************************************************************************************************/
void MainWindow::MainWin_bluetoothSlotDeviceDiscovered(QString name)
{
//    qDebug() << "MainWin_bluetoothSlotDeviceDiscovered  called";

    ui->BLU_ConnectButton->setEnabled(true);
    ui->BLU_DetectedDeviceComboBox->setEnabled(true);

    ui->BLU_StatusLabel->setText("State:NewDevDet");

    ui->BLU_DetectedDeviceComboBox->addItem(name);

    QString AutoConnDevName = ui->BLU_AutoConnDevNameL->text();

    if( name == AutoConnDevName && ui->BLU_AutoConnCheckBox->isChecked() )
    {
        ui->BLU_DetectedDeviceComboBox->setCurrentIndex( ui->BLU_DetectedDeviceComboBox->count() - 1 );

        ui->DebugDataTable->insertRow(ui->DebugDataTable->rowCount() );
        ui->DebugDataTable->setItem(ui->DebugDataTable->rowCount() -1 ,4,
                                    new QTableWidgetItem(QString("DevNameMatched:Connecting ") ));

        emit MainWin_bluetootSignalConnectToDeviceByName(AutoConnDevName);
    }
    else
    {
        ui->statusbar->showMessage("Please select BLE device",1000);
    }
}

void MainWindow::MainWin_bluetoothSlotDiscoveryFinished(void)
{
    ui->BLU_ConnectButton->setEnabled(true);
    ui->BLU_ScanButton->setEnabled(true);
    ui->BLU_DetectedDeviceComboBox->setEnabled(true);

    ui->statusbar->showMessage("DiscoveryFinished",1000);
//    ui->BLU_StatusLabel->setText("DiscoveryFinished");
}

void MainWindow::MainWin_bluetoothSlotConnectingStart()
{
    ui->BLU_StatusLabel->setText("State:Connecting");
    ui->statusbar->showMessage("Connecting to device...",1000);
}

void MainWindow::MainWin_bluetoothSlotConnectionEstablished(void)
{
    ui->statusbar->showMessage("Aquire data",1000);

    ui->BLU_StatusLabel->setText("State:ConnReadyAcqData");
    QVariant variant= QColor (220,255,220);
    QString colcode = variant.toString();
    ui->BLU_StatusLabel->setAutoFillBackground(true);
    ui->BLU_StatusLabel->setStyleSheet("QLabel { background-color :"+colcode+" ; color : black; }");

    if(false == NvM_DataLoadedFromExternalSourceFlag)
    {
        NvM_DataLoadedFromExternalSourceFlag = true;
        ReadNvMDataFromLineFollower();
    }

}

void MainWindow::MainWin_bluetoothSlotConnectionInterrupted(void)
{

    ui->statusbar->showMessage("Connection interrupted, why?",1000);


    ui->BLU_StatusLabel->setText("State:Disconnected");
    QVariant variant= QColor (255,255,255);
    QString colcode = variant.toString();
    ui->BLU_StatusLabel->setAutoFillBackground(true);
    ui->BLU_StatusLabel->setStyleSheet("QLabel { background-color :"+colcode+" ; color : black; }");
}

void MainWindow::on_BLU_ScanButton_clicked()
{
    ui->BLU_StatusLabel->setText("State:Scanning");
    ui->BLU_DetectedDeviceComboBox->clear();
    ui->BLU_ConnectButton->setEnabled(false);
    ui->BLU_ScanButton->setEnabled(false);
    ui->BLU_DetectedDeviceComboBox->setEnabled(true);
    ui->statusbar->showMessage("Searching for bluetooth devices...",1000);
    emit MainWin_bluetoothSignalStartDiscoveryDevices();
}

void MainWindow::on_BLU_ConnectButton_clicked()
{
    QString NewAutoConnDevName = ui->BLU_DetectedDeviceComboBox->itemText(ui->BLU_DetectedDeviceComboBox->currentIndex());
    ui->BLU_AutoConnDevNameL->setText(NewAutoConnDevName);
    emit MainWin_bluetootSignalConnectToDeviceByName(NewAutoConnDevName);
}

void MainWindow::on_BLU_DisconnectButton_clicked()
{

    on_BLU_RobotStop_Button_clicked();
    QThread::msleep(30);
    on_BLU_RobotStop_Button_clicked();
    QThread::msleep(30);
    on_BLU_RobotStop_Button_clicked();
    emit MainWin_bluetoothDisconnect();

    ui->BLU_StatusLabel->setText("State:Disconnected");
    ui->BLU_ConnectButton->setEnabled(true);
    ui->BLU_ScanButton->setEnabled(true);
    QVariant variant= QColor (255,255,255);
    QString colcode = variant.toString();
    ui->BLU_StatusLabel->setAutoFillBackground(true);
    ui->BLU_StatusLabel->setStyleSheet("QLabel { background-color :"+colcode+" ; color : black; }");
}


/***************************************************************************/
/***************************************************************************/
/***************************************************************************/
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

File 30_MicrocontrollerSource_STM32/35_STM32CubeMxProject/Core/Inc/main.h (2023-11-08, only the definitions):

#define TIM15_CH1_MotPWM1_1_Pin GPIO_PIN_5
#define TIM15_CH1_MotPWM1_1_GPIO_Port GPIOE
#define TIM15_CH2_MotPWM1_2_Pin GPIO_PIN_6
#define TIM15_CH2_MotPWM1_2_GPIO_Port GPIOE
#define LD1_Pin GPIO_PIN_1
#define LD1_GPIO_Port GPIOC
#define LD2_Pin GPIO_PIN_2
#define LD2_GPIO_Port GPIOC
#define SenD1_Pin GPIO_PIN_12
#define SenD1_GPIO_Port GPIOE
#define SenD2_Pin GPIO_PIN_13
#define SenD2_GPIO_Port GPIOE
#define VL53_INT_Pin GPIO_PIN_14
#define VL53_INT_GPIO_Port GPIOE
#define VL53_INT_EXTI_IRQn EXTI15_10_IRQn
#define VL53_XSHUT_Pin GPIO_PIN_15
#define VL53_XSHUT_GPIO_Port GPIOE
#define I2C2_SCL_VL53_Pin GPIO_PIN_10
#define I2C2_SCL_VL53_GPIO_Port GPIOB
#define I2C2_SDA_VL53_Pin GPIO_PIN_11
#define I2C2_SDA_VL53_GPIO_Port GPIOB
#define IR_PIN_INPUT_Pin GPIO_PIN_12
#define IR_PIN_INPUT_GPIO_Port GPIOB
#define IR_PIN_INPUT_EXTI_IRQn EXTI15_10_IRQn
#define TIM12_CH1_MotPWM2_2_Pin GPIO_PIN_14
#define TIM12_CH1_MotPWM2_2_GPIO_Port GPIOB
#define TIM12_CH2_MotPWM2_1_Pin GPIO_PIN_15
#define TIM12_CH2_MotPWM2_1_GPIO_Port GPIOB
#define USER_BUTTON_Pin GPIO_PIN_12
#define USER_BUTTON_GPIO_Port GPIOA
#define LDD1_Pin GPIO_PIN_15
#define LDD1_GPIO_Port GPIOA
#define BLU_ABN_MEM_Pin GPIO_PIN_3
#define BLU_ABN_MEM_GPIO_Port GPIOD
#define BLU_RESET_Pin GPIO_PIN_4
#define BLU_RESET_GPIO_Port GPIOD
#define EEPROM_WC_Pin GPIO_PIN_0
#define EEPROM_WC_GPIO_Port GPIOE
#define MPU6050_INT_Pin GPIO_PIN_1
#define MPU6050_INT_GPIO_Port GPIOE

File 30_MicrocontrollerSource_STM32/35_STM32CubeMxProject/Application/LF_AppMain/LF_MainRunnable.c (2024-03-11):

#include "EEmu.h"
#include "LedMngr.h"
#include "Irda.h"
#include "EncodersHandler.h"
#include "LinePosEstimator.h"

#include "LF_Menager.h"
#include "BluetoothClassicComm.h"

#include "stm32h7xx_it.h"

#define MEAS_ENABLE 1
#define MEAS_DISABLE 0
#define MEASURE_EXECUTION_TIME MEAS_DISABLE
/* In cases, when I was sending few debug logs, longest exeuction time has been around ~0.5ms
* If you planning send more debug logs, then usage of RTOS, or any other time execution managment strategy may be required
*/

/** @brief LF_AppTask
*  @details Called one time after power on cycle from main function (file main.c)
*/
void LF_AppInit(void)
{
	/*Hardware peripherials are already initialized in "main.c"*/

	EE_Init();	 /*EEPROM Emulation module init*/
	BLU_Init();  /*Bluetooth low energy module init*/
	IR_Init();
	LED_Init();  /*Led module init*/
	ENC_Init();  /*Encoder module init*/
	LPE_Init();  /*Line Position estimator init*/

	/*Line Following App functions*/
	LF_MngrInit();
}


/** @brief LF_AppTask
*   @details Called continously from an infinity loop in main function (file main.c)
*/
void LF_AppTask(void) //only one Task without any RTOS, all works fine -- for now this solution is inaf :)
{
#if MEASURE_EXECUTION_TIME == MEAS_ENABLE
	static uint32_t ExecutionTimerLogIntervalTimer = 0U;
	static uint32_t ExectionMeasureTimerStart=0,ExectionMeasureTimerEnd = 0;
	static uint32_t LongestExecutionTime = 0;
	static uint32_t LongestExecutionTimeStamp = 0;
	static float AverageExecTime = 0.0F;
	static uint32_t LoopCounter = 0;
	ExectionMeasureTimerStart = HAL_GetTick100us();
	LoopCounter++;
#endif //MEASURE_EXECUTION_TIME

	{
		{
			LED_MngrTask();
			BLU_Task();
			IR_Task();
			LPE_Task();
			ENC_Task();

			/*Highest layer Line Follower Application Task: */
			LF_MngrTask(); /*Line Following Menager task */
		}
	}

#if MEASURE_EXECUTION_TIME == MEAS_ENABLE
	ExectionMeasureTimerEnd = HAL_GetTick100us();
	if( (ExectionMeasureTimerEnd - ExectionMeasureTimerStart) >= LongestExecutionTime){
		LongestExecutionTime = (ExectionMeasureTimerEnd - ExectionMeasureTimerStart);
		LongestExecutionTimeStamp = HAL_GetTick100us();
	}

	AverageExecTime = AverageExecTime + ( (1.0F/LoopCounter) * 
									(ExectionMeasureTimerEnd - ExectionMeasureTimerStart)  - ((AverageExecTime) ) );
	
	if(HAL_GetTick() - ExecutionTimerLogIntervalTimer > 5000){
		ExecutionTimerLogIntervalTimer = HAL_GetTick();
		BLU_DbgMsgTransmit("Longesst ExecTime: %.2fms TimeStamp:%.2fms Average: %f",(float)LongestExecutionTime/10,(float)LongestExecutionTimeStamp/10, AverageExecTime);
		LongestExecutionTime = 0;
		LoopCounter = 0;
		AverageExecTime = 0;
	}
#endif // MEASURE_EXECUTION_TIME
}

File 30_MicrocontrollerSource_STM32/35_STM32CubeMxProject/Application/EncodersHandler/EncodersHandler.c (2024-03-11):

/*
 * EncodersHandler.c
 *
 *  Created on: Jan 11, 2021
 *      Author: Teodor
 */
#include "stm32h7xx_it.h"

#include "EncodersHandler.h"
#include "LF_AppConfig.h"
#include "EEmu.h"

#include "math.h"

#include "tim.h"
#include "../BluetoothComm/BluetoothClassicComm.h"


/*************************************************************************************/
/*************************************************************************************/
/*************************************************************************************/

#ifndef M_PI
#define M_PI		3.14159265358979323846
#endif 

#define LeftEncoderCnt htim8.Instance->CNT
#define RightEncoderCnt htim4.Instance->CNT


/*************************************************************************************/
/*************************************************************************************/
/*************************************************************************************/

typedef struct PositionStruct_t
{
	float X; 
	float Y;
	float O; /*Orientation / angle */
	float prX;
	float prY;
	float prO;
}PositionStruct_t;


typedef struct EncHandlerDescr_t
{
	uint16_t* LeftEncoderCntImpulsCount;
	uint16_t* RightEncoderCntImpulsCount;

	float Distance_LeftWheel;
	float Distance_RightWheel;
	uint32_t ProbeCounter;
	uint16_t PreviousLeftEncoderCntImpulsCount;
	uint16_t PreviousRightEncoderCntImpulsCount;

	float NVM_WheelBase;
	float NVM_OneImpulsDistance;


	float LeftWheelSpeed;
	float RightWheelSpeed;

	float LineFollowerSpeed;

	float TakenDistance;
	float AverageSpeed;

	float yawRateWheelBased;

}Encoders_Module_t ;

Encoders_Module_t EncHandlerDescr = {.ProbeCounter = 1};
PositionStruct_t RobotPosition = {0};

/*************************************************************************************/
/*************************************************************************************/
/*************************************************************************************/
/* @brief
 * Equations for determining the position and orientation of the robot based on the collected information.
 * ref: https://github.com/trteodor/FAST_Line_Follower_STM32H7/blob/master/docs/LF_Desc_PL.pdf
 * equasition, page 21: 3.12
 */
static void EsimtateRobotOrientationAndPosition(void)
{
	RobotPosition.O=RobotPosition.prO +
			( (1/EncHandlerDescr.NVM_WheelBase) *(EncHandlerDescr.Distance_LeftWheel - EncHandlerDescr.Distance_RightWheel) );

	RobotPosition.X=RobotPosition.prX+(  0.5*cos(RobotPosition.prO) *
			( EncHandlerDescr.Distance_LeftWheel + EncHandlerDescr.Distance_RightWheel ) );

	RobotPosition.Y=RobotPosition.prY+ (  0.5*sin(RobotPosition.prO) *
			           ( EncHandlerDescr.Distance_LeftWheel + EncHandlerDescr.Distance_RightWheel ) );

	RobotPosition.prX = RobotPosition.X;
	RobotPosition.prY = RobotPosition.Y;
	RobotPosition.prO = RobotPosition.O;
}

static void CalculateBasicBasedOnEncodersData(void)
{
	EncHandlerDescr.ProbeCounter++;

	/*uint overflow isn't problem becuse for example 2-255=3 so diffrent is 3 that's true*/
	uint16_t TmpLeftEncImpCnt= UINT16_MAX - *EncHandlerDescr.LeftEncoderCntImpulsCount;
	uint16_t TmpRightEncImpCnt= UINT16_MAX - *EncHandlerDescr.RightEncoderCntImpulsCount;


	int16_t DifferenceValueLeft;
	int16_t DifferenceValueRight;

	DifferenceValueLeft = TmpLeftEncImpCnt-EncHandlerDescr.PreviousLeftEncoderCntImpulsCount;
	DifferenceValueRight = TmpRightEncImpCnt-EncHandlerDescr.PreviousRightEncoderCntImpulsCount;

	EncHandlerDescr.Distance_LeftWheel=((DifferenceValueLeft)*EncHandlerDescr.NVM_OneImpulsDistance);

	EncHandlerDescr.Distance_RightWheel = ((DifferenceValueRight)*EncHandlerDescr.NVM_OneImpulsDistance);

	EncHandlerDescr.LeftWheelSpeed = EncHandlerDescr.Distance_LeftWheel/EncodersProbeTimeInSeconds;
	EncHandlerDescr.RightWheelSpeed = EncHandlerDescr.Distance_RightWheel/EncodersProbeTimeInSeconds;

	/*Estimate LineFollower speed*/
	EncHandlerDescr.LineFollowerSpeed= (EncHandlerDescr.LeftWheelSpeed + EncHandlerDescr.RightWheelSpeed) / 2;

	/*Integral of speed is equal distance*/
	EncHandlerDescr.TakenDistance += ( (EncHandlerDescr.LineFollowerSpeed /2) * EncodersProbeTimeInSeconds ) ;


	/*Estimage Average speed  Xav[n] = Xav[n-1] + (1/n)*(Zn-Xav[n-1])   */
	EncHandlerDescr.AverageSpeed += ( (float)(1.0F/EncHandlerDescr.ProbeCounter) *
									  	   (EncHandlerDescr.LineFollowerSpeed - EncHandlerDescr.AverageSpeed) );

	/* Save current data as previos (input handled)*/
	EncHandlerDescr.PreviousLeftEncoderCntImpulsCount=TmpLeftEncImpCnt;
	EncHandlerDescr.PreviousRightEncoderCntImpulsCount=TmpRightEncImpCnt;

	/*Turning right - positive values*/
	EncHandlerDescr.yawRateWheelBased = ((( (EncHandlerDescr.RightWheelSpeed - EncHandlerDescr.LeftWheelSpeed) ) / EncHandlerDescr.NVM_WheelBase) / M_PI);


}






static void ReadNvMParameters(void)
{
	EE_ReadVariableF32(EE_NvmAddr_EncodersOneImpDistance_F32, &EncHandlerDescr.NVM_OneImpulsDistance);
	EE_ReadVariableF32(EE_NvmAddr_EncodersWheelBaseInfo_F32, &EncHandlerDescr.NVM_WheelBase);
}

static void BleEncUpdateNvmDataCallBack(void)
{
	ReadNvMParameters();
}

static void UpdateEncBleDataReport(void)
{

	BLU_MapDataReport_t BLE_MapDataReport = {0};

	BLE_MapDataReport.WhLftSp = EncHandlerDescr.LeftWheelSpeed;
	BLE_MapDataReport.WhRhtSp = EncHandlerDescr.RightWheelSpeed;
	BLE_MapDataReport.PosX = RobotPosition.X;
	BLE_MapDataReport.PosY = RobotPosition.Y;
	BLE_MapDataReport.PosO = RobotPosition.O;
	BLE_MapDataReport.TravelledDistance = EncHandlerDescr.TakenDistance;
	BLE_MapDataReport.YawRate = EncHandlerDescr.yawRateWheelBased;

	BLU_ReportMapData(&BLE_MapDataReport);
}
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

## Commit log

2023-06-13 Init Line Follower Light repo - copy old project
    [Asembly MotorEncoderWheel.SLDASM, BatteryHolder.SLDPRT, BatteryHolder_Full.STL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]
2023-06-20 REPO: Update directories names for better readability
    [Asembly MotorEncoderWheel.SLDASM, BatteryHolder.SLDPRT, BatteryHolder_Full.STL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]
2023-06-25 QT: Not fully but satisfied communiation prototype with MCU
2023-06-25 QT: FIX Bluetooth Connection interface - disconnect device while app closing
    [mainwindow.cpp]
2023-06-27 QT: Add dark theme as a test and YawRate graph
2023-07-09 QT: Add Data NVM Error Data Weigth Receive handler
    [BleDataManager.cpp, mainwindow.cpp]
2023-07-13 QT:MCU: Fix NvM Data update
    [BLE_Comm.c, BleDataManager.cpp, mainwindow.cpp]
2023-07-15 MCU: Code rework begin
    [BLE_Comm.c, BleDataManager.cpp, EncodersHandler.c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]
2023-07-16 Basic Encoder Handler Ready
2023-07-16 QT:MCU: Add position orientation to Base Frame
2023-07-20 MCU:QT: Add motors factors config in QT App
2023-07-31 HW: Main board re work start for Bluetooth Classic
    [8205A.SchLib, BasicComponents.PcbLib, BasicComponents.SCHLIB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]
2023-08-01 HW: update continue
    [LF_Light_BluClassic.SchDoc]
2023-08-03 HW: Quick redesign of Main Board
    [1_PowerInput.SchDoc, 2_Microcontroller.SchDoc, 3_MotorDrivers.SchDoc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]
2023-08-03 3D: Start new assembly development
    [Asembly MotorEncoderWheel.SLDASM, BatteryHolder.SLDPRT, BatteryHolder_Full.STL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]
2023-08-08 3D: Very frist new Working version of highest assebmly
    [BatterHolderCl.SLDPRT, BatteryHolder.SLDPRT, BatteryHolder.STL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]
2023-08-08 HW: Ready to order new main board
    [1_PowerInput.SchDoc, 2_Microcontroller.SchDoc, LF_Light_MainBoard_BluClassic.PrjPcb]
2023-08-09 Revert:MCU: Restore accidental changes
    [LF_Light_MainBoard_BluClassic.PrjPcb]
2023-08-17 QT: Add Feature: save and load plot data buttons
2023-08-20 MCU:Add Docs, Vs_CodeDebug,UartReceiveToIdle
2023-08-22 QT:MCU: Simple Bluetooth communication fix
    [BluetoothClassicComm.c, mainwindow.cpp]
2023-08-24 3D: Update a bit MB SB connector
    [BatteryHolder.SLDPRT, BatteryHolder.STL, JumpLiftProtector.SLDPRT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]
2023-08-24 3D: Update MB SB Connector dimensions
    [LF_MB_SB_ConnectorAsm.SLDPRT, LF_MB_SB_ConnectorAsm.STL]
2023-08-25 MCU: Revert adaptation for new HW
    [LF_Menager.c]
2023-08-25 MCU: Adapt to new STM32_CubeMX
2023-08-26 3D:MCU: New HW ready for development continuation!
    [LF_MB_SB_ConnectorAsm.SLDPRT, LF_MB_SB_ConnectorAsm.STL]
2023-08-26 MCU: Stright line detection very frist prototype
2023-08-31 MCU: Track event handling very frist prototype
2023-10-09 MCU: Add start LF by user button
2023-10-11 MCU: Add Line Pid reporter function
2023-11-02 3D: Adapt for new Jsumo tire based wheels
    [BatteryHolder.SLDPRT, BatteryHolderJsumo.STL, JSumoTireWheel.SLDPRT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]
2023-11-05 3D: continuation of adaptation for JSumo tires
    [JSummoWheelAsm.SLDASM, JSumoTireWheel.SLDPRT, JSumoTireWheel.STL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]
2023-11-08 MCU: Prototype Right Angle Hndlr: Use PID regulator based on the line postion
2023-11-08 MCU: Add Infreated receiver driver prototype
2023-11-10 MCU:QT: Align NvM params to new rAg Pid regulator
2023-11-14 MCU: Fix Right angle PID
    [LF_Menager.c]
2025-07-11 Add display case
    Add display case

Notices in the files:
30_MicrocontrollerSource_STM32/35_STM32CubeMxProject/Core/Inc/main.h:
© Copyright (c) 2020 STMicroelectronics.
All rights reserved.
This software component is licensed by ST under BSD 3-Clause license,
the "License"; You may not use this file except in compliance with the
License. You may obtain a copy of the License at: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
